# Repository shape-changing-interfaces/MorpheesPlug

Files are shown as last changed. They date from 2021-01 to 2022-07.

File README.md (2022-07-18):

# MorpheesPlug

MorpheesPlug is a toolkit to prototype shape-changing interfaces, which are physical interfaces they can change their shapes and/or accept deformation as an input as an interaction method with users [1,2,3]. MorpheesPlug is built based on shape-changing interface taxonomies [4,5]. The design process and example applications of MorpheesPlug can be found in our publication at ACM [6].

[1] Marcelo Coelho and Jamie Zigelbaum. 2011. Shape-changing interfaces. Personal Ubiquitous Comput. 15, 2 (February 2011), 161–173. DOI:https://doi.org/10.1007/s00779-010-0311-y

[2] Majken K. Rasmussen, Esben W. Pedersen, Marianne G. Petersen, and Kasper Hornbæk. 2012. Shape-changing interfaces: a review of the design space and open research questions. In Proceedings of the SIGCHI Conference on Human Factors in Computing Systems (CHI '12). Association for Computing Machinery, New York, NY, USA, 735–744. DOI:https://doi.org/10.1145/2207676.2207781

[3] Jason Alexander, Anne Roudaut, Jürgen Steimle, Kasper Hornbæk, Miguel Bruns Alonso, Sean Follmer, and Timothy Merritt. 2018. Grand Challenges in Shape-Changing Interface Research. In Proceedings of the 2018 CHI Conference on Human Factors in Computing Systems (CHI '18). Association for Computing Machinery, New York, NY, USA, Paper 299, 1–14. DOI:https://doi.org/10.1145/3173574.3173873

[4] Anne Roudaut, Abhijit Karnik, Markus Löchtefeld, and Sriram Subramanian. 2013. Morphees: toward high "shape resolution" in self-actuated flexible mobile devices. In Proceedings of the SIGCHI Conference on Human Factors in Computing Systems (CHI '13). Association for Computing Machinery, New York, NY, USA, 593–602. DOI:https://doi.org/10.1145/2470654.2470738

[5] Hyunyoung Kim, Celine Coutrix, and Anne Roudaut. 2018. Morphees+: Studying Everyday Reconfigurable Objects for the Design and Taxonomy of Reconfigurable UIs. In Proceedings of the 2018 CHI Conference on Human Factors in Computing Systems (CHI '18). Association for Computing Machinery, New York, NY, USA, Paper 619, 1–14. DOI:https://doi.org/10.1145/3173574.3174193

[6] Hyunyoung Kim, Aluna Everitt, Carlos Tejada, Mengyu Zhong, and Daniel Ashbrook. 2021. MorpheesPlug: A Toolkit for Prototyping Shape-Changing Interfaces. In Proceedings of the 2021 CHI Conference on Human Factors in Computing Systems (CHI '21). Association for Computing Machinery, New York, NY, USA, Article 101, 1–13. https://doi.org/10.1145/3411764.3445786

## Authors
<ul>
<li>Hyunyoung Kim</li>
<li>Aluna Everitt</li>
<li>Carlos E. Tejada</li>
<li>Mengyu Zhong</li>
<li>Daniel Ashbrook</li>
</ul>

## Folders
<ul>
  <li>Module_Eagle: control module board Eagle files.</li>
  <li>Module_Enclosure: Enclosure stl files for control module.</li>
  <li>MorpheesPlug: Autodesk Fusion 360 add-in to design widgets.</li>
</ul>

## How to install the MorpheesPlug add-in on Autodesk Fusion 360
1. Download and place the [MorpheesPlug subfolder](./MorpheesPlug) under ~/Library/Application Support/Autodesk/Autodesk Fusion 360/API/Scripts/ (Mac).
2. Launch Fusion 360.
3. Go to Tools panel then click ADD-INS icon.
4. Click MorpheesPlug Script under My Scripts.
5. Click Run.
6. Choose a widget and change the parameters as needed.
Note: If you want to show the script icon on your Fusion 360, put the folder under ~/Library/Application Support/Autodesk/Autodesk Fusion 360/API/AddIns/ (Mac). The icon will show up under Tools/Add-ins arrow. You can click the icon to launch the script.

## License
[MIT](https://choosealicense.com/licenses/mit/)

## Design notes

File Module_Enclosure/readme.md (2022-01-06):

1. The Connector should be SLA printed with flexible material to ensure airtight connection. We used Formlabs Flexible 80A.

2. The other parts can be printed with any hard thermoplastic. We used PLA.

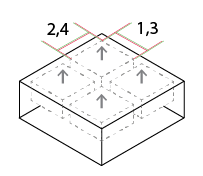
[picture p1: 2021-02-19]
MorpheesPlug/Resources/Widget_Image/Bump.png

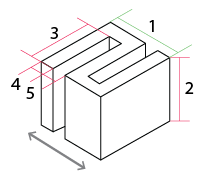
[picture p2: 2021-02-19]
MorpheesPlug/Resources/Widget_Image/Fold.png

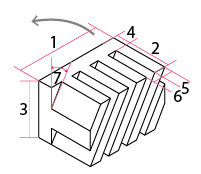
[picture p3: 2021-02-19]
MorpheesPlug/Resources/Widget_Image/Teeth.png

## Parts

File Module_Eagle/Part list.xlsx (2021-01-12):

Part | Value | Device | Package | Description | POPULARITY | PROD_ID | SF_ID | SF_SKU | VALUE | In the basket
C1 | 0.1uF | 0.1UF-KIT-EZ-50V-20% | CAP-PTH-SMALL-KIT | 0.1µF ceramic capacitors |  | CAP-08370 |  |  | 0.1uF |  | Test with the capacitor kit, fill in the kit later.
D1 | 1N4007 | DIODE-1N4148 | DIODE-1N4148 | Diode |  | DIO-08378 |  |  | 200mA/100V/1V | y
D2 | 1N4007 | DIODE-1N4148 | DIODE-1N4148 | Diode |  | DIO-08378 |  |  | 200mA/100V/1V | y | 1N4007 Ensretter 1000V 1A DO41
J1 | POWER_JACK | POWER_JACK | POWER_JACK_PTH | Power Jack Connector |  | CONN-08197 |  |  |  | y
Q1 | TIP120 | BD679 | TO126AV | NPN DARLINGTON TRANSISTOR | 0 |  |  |  |  | y
Q2 | TIP120 | BD679 | TO126AV | NPN DARLINGTON TRANSISTOR | 0 |  |  |  |  | y
R1 | 220R | R-US_0207/10 | 0207/10 | RESISTOR, American symbol |  |  |  |  |  | y
R2 | 220R | R-US_0207/10 | 0207/10 | RESISTOR, American symbol |  |  |  |  |  | y
R3 | 10kR | R-US_0207/10 | 0207/10 | RESISTOR, American symbol |  |  |  |  |  | y
R4 | 10kR | R-US_0207/10 | 0207/10 | RESISTOR, American symbol |  |  |  |  |  | y
S1-6.0MM | Switch1 | MOMENTARY-SWITCH-SPST-PTH-6.0MM | TACTILE_SWITCH_PTH_6.0MM | Momentary Switch (Pushbutton) - SPST |  | SWCH-08441 |  | COM-00097 |  | y
S2-6.0MM | Switch2 | MOMENTARY-SWITCH-SPST-PTH-6.0MM | TACTILE_SWITCH_PTH_6.0MM | Momentary Switch (Pushbutton) - SPST |  | SWCH-08441 |  | COM-00097 |  | y
U$1 | TRINKET-M0 | TRINKET-M0 | TRINKET-M0 | Adafruit Trinket M0 |  |  |  |  |  | y
U$2 | ADP51* | ADP51* | ADP5121 | Panasonic pressure sensor series |  |  |  |  |  | y
VAL/IN |  | CONN_02POLAR | MOLEX-1X2 | Multi connection point. Often used as Generic Header-pin footprint for 0.1 inch spaced/style header connections |  |  | PRT-09918 |  |  | y
VALVE/OUT |  | CONN_02POLAR | MOLEX-1X2 | Multi connection point. Often used as Generic Header-pin footprint for 0.1 inch spaced/style header connections |  |  | PRT-09918 |  |  | y

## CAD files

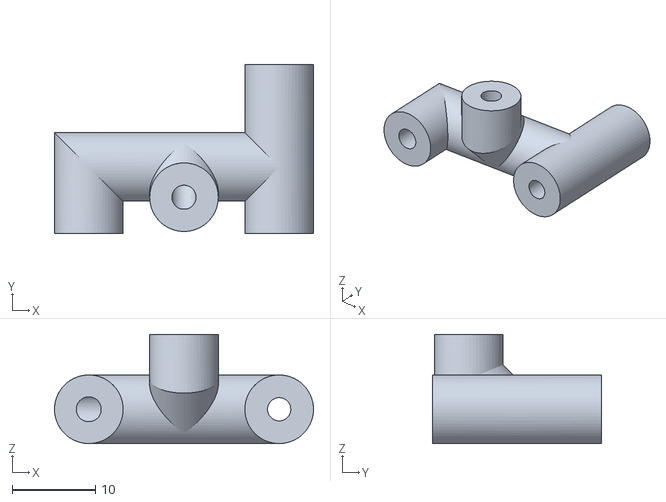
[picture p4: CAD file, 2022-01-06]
Module_Enclosure/Connector_SLA printing.stl
31.2 x 20.3 x 13.1

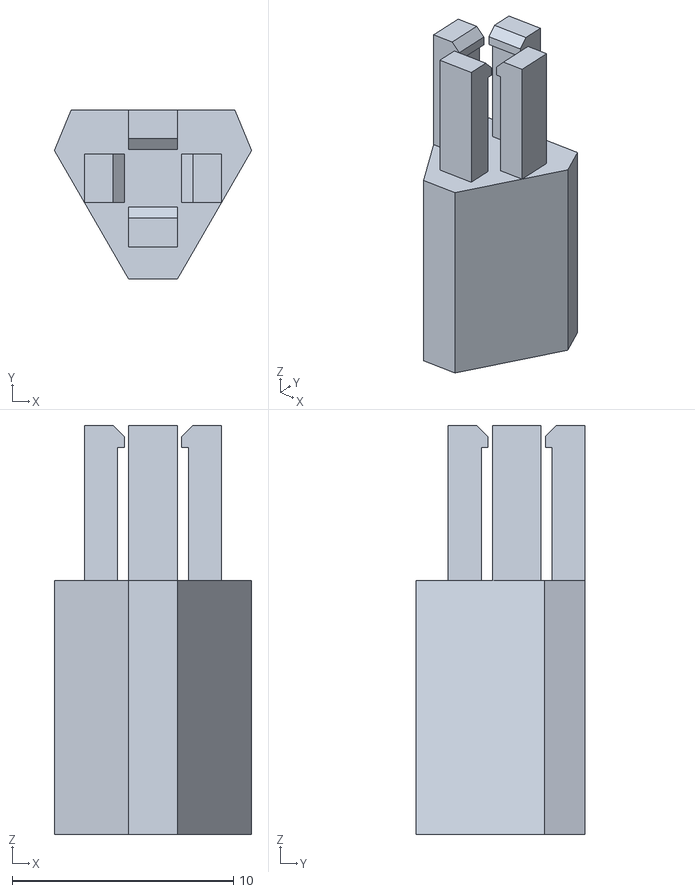
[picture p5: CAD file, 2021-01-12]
Module_Enclosure/Switch cap v4.stl
8.92 x 7.66 x 18.5

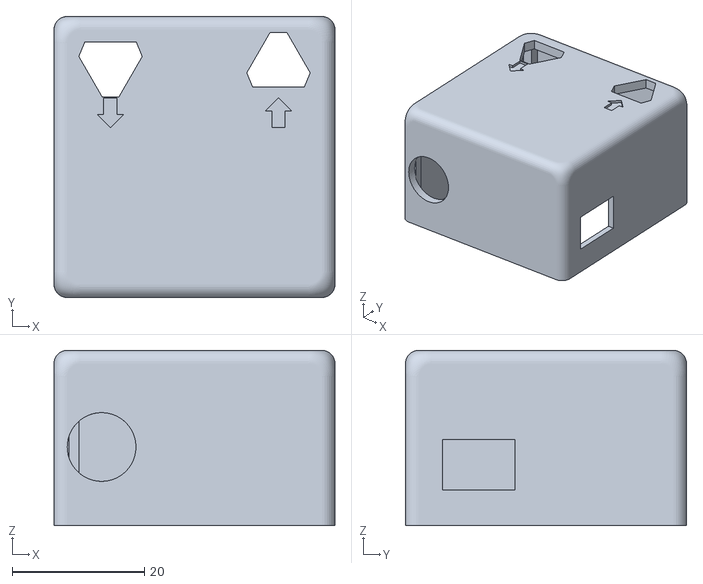
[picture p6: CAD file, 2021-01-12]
Module_Enclosure/Enclosure top v3.stl
42.5 x 42.5 x 26.5

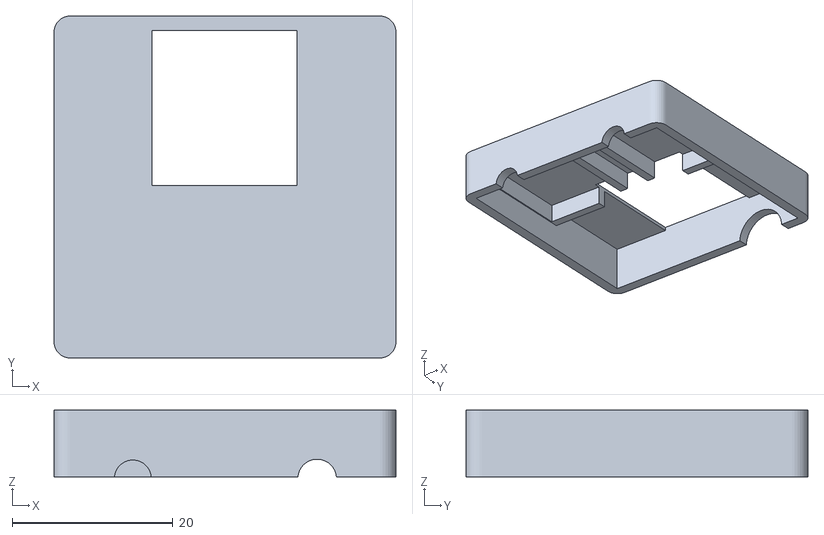
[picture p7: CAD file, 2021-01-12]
Module_Enclosure/Enclosure middle v4.stl
42.5 x 42.5 x 8.30

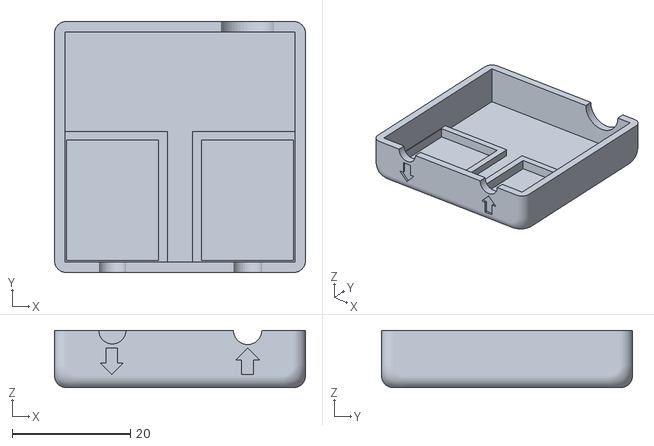
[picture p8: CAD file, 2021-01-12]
Module_Enclosure/Enclosure bottom v5.stl
42.5 x 42.5 x 9.70

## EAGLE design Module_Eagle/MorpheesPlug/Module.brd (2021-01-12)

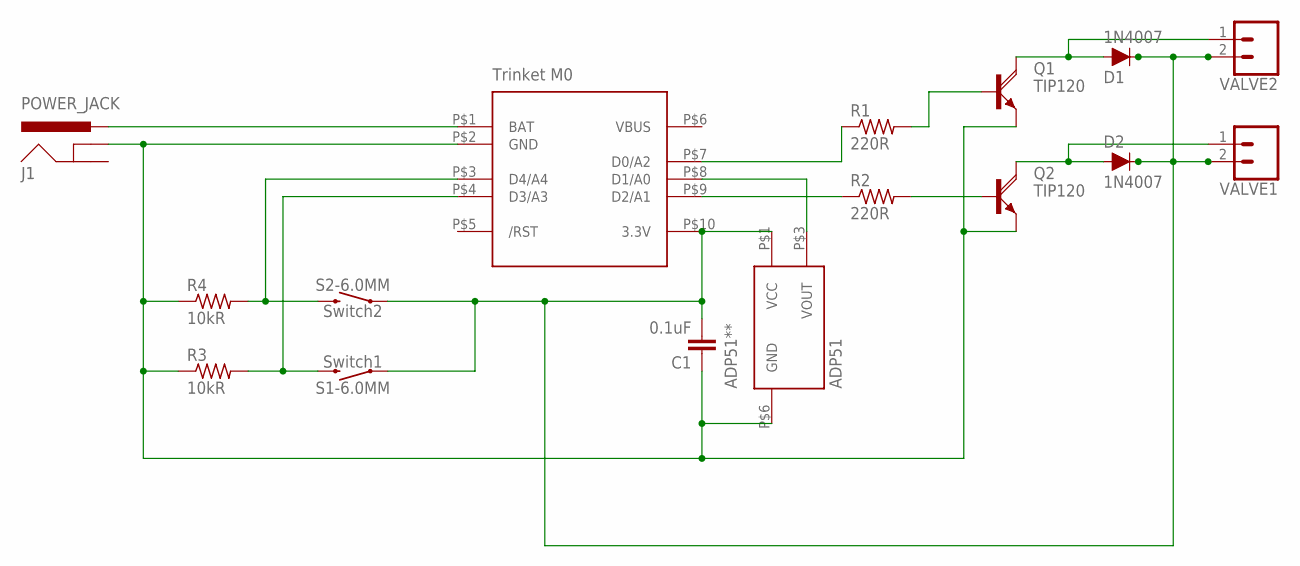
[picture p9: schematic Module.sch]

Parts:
C1: 0.1uF; CAP-PTH-SMALL-KIT
D1, D2: 1N4007; DIODE-1N4148
J1: POWER_JACK; POWER_JACK_PTH
Q1, Q2: TIP120; TO126AV
R1, R2: 220R; 0207/10
R3, R4: 10kR; 0207/10
S1-6.0MM: Switch1; TACTILE_SWITCH_PTH_6.0MM
S2-6.0MM: Switch2; TACTILE_SWITCH_PTH_6.0MM
U$1: TRINKET-M0
U$2: ADP51; ADP5121
VALVE1, VALVE2: CONN_02POLAR; MOLEX-1X2

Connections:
unnamed: J1.PWR, U$1.P$1 (BAT)
unnamed: C1.2, D1.C, D2.C, S1-6.0MM.1, S2-6.0MM.1, U$1.P$10 (3.3V), U$2.P$1 (VCC), VALVE1.2, VALVE2.2
unnamed: R4.2, S2-6.0MM.3 (2), U$1.P$3 (D4/A4)
unnamed: R3.2, S1-6.0MM.3 (2), U$1.P$4 (D3/A3)
unnamed: Q1.B, R1.2
unnamed: Q2.B, R2.2
unnamed: R1.1, U$1.P$7 (D0/A2)
unnamed: R2.1, U$1.P$9 (D2/A1)
unnamed: D1.A, Q1.C, VALVE2.1
unnamed: D2.A, Q2.C, VALVE1.1
unnamed: C1.1, J1.GNDBREAK, Q1.E, Q2.E, R3.1, R4.1, U$1.P$2 (GND), U$2.P$6 (GND)
unnamed: U$1.P$8 (D1/A0), U$2.P$3 (VOUT)

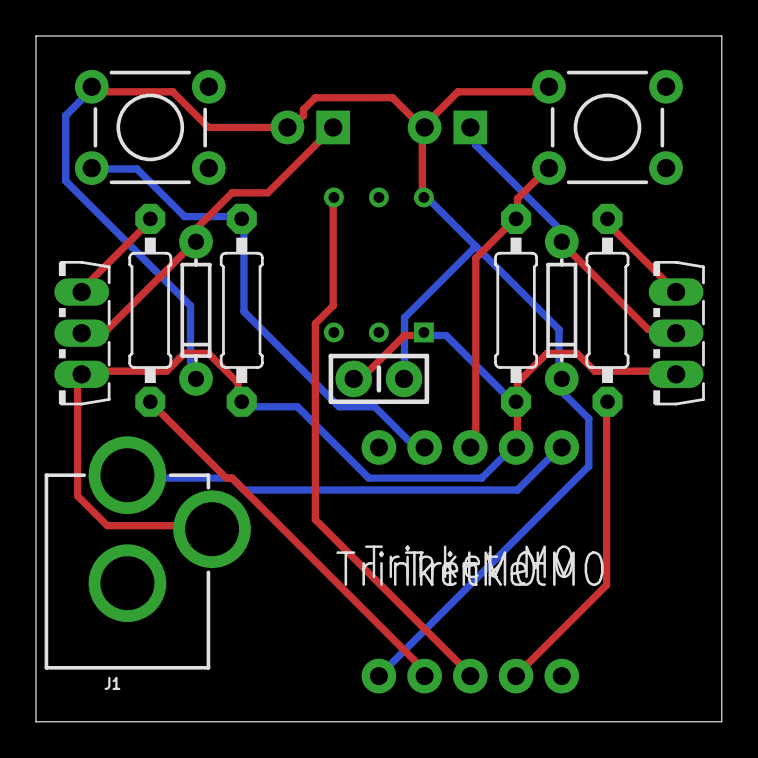
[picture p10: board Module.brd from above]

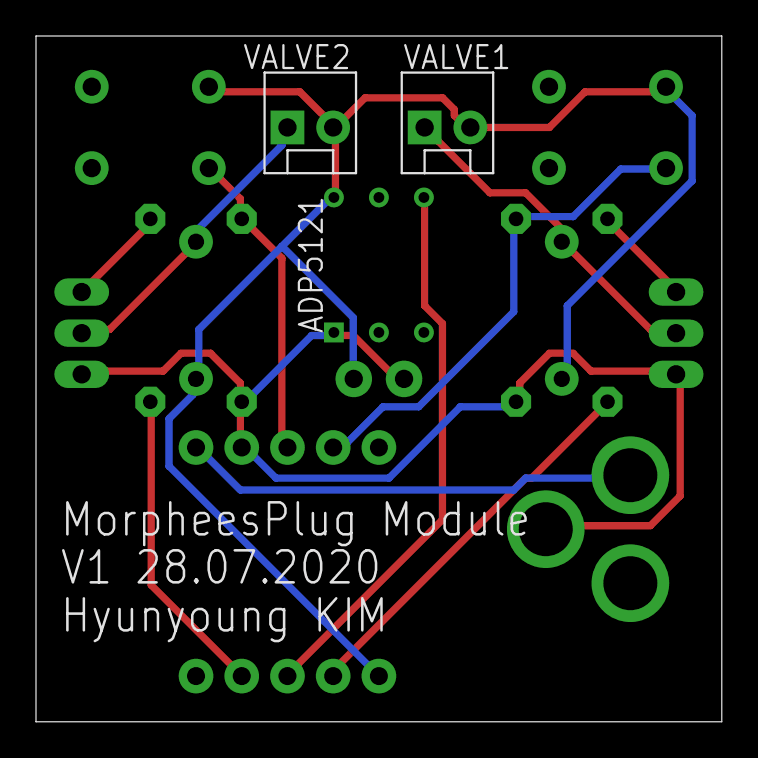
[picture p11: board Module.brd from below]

Board: 2 copper layers, 38.1 x 38.1 mm, 16 parts (3 on the bottom side), 12 nets.

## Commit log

2021-01-12 Initial commit, control module board Eagle files
    [Module.brd, Module.sch, Part list.xlsx]
2021-01-12 Initial commit. Control module enclosure 3D models
    [Enclosure bottom v2.stl, Enclosure bottom v3.stl, Enclosure bottom v4.stl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]
2022-01-06 Added forgotten stl file
    [Connector_SLA printing.stl]
2022-01-06 Add forgotten connector stl file.
    [Connector_SLA printing.stl]
2022-01-06 Moved to Enclosure folder
    [Connector_SLA printing.stl]
2022-01-06 Add explanation how to print the models

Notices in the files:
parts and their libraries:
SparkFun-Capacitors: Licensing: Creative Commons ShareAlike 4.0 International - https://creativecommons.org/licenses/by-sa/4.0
